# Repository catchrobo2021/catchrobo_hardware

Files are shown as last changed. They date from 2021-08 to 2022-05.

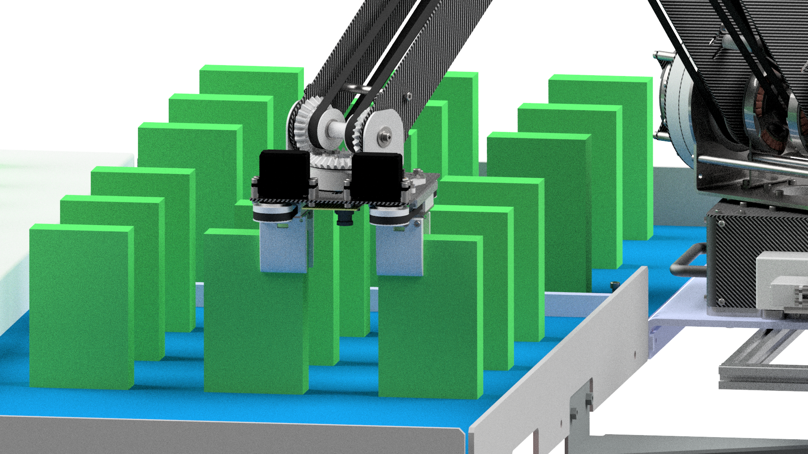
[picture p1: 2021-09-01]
images/assy-robot_with_field_capt2.png

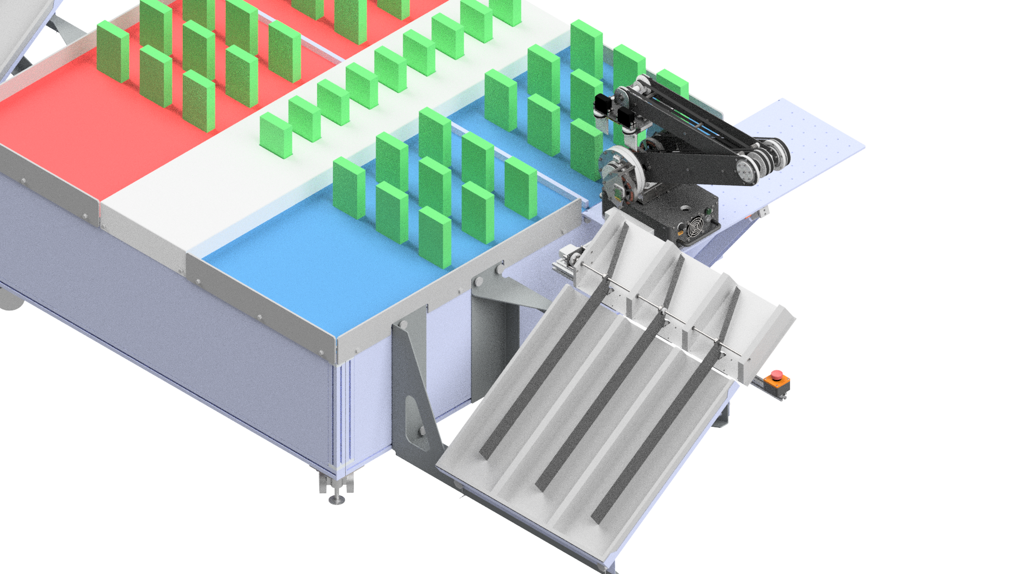
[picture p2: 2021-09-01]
images/assy-robot_with_field_robot_safety.png

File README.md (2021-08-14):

# Catchrobo 2021 Hardware
## 仕様
| | | | J1 | J2 | J3 | J4 | J5 | gripper |
|---|---|---|---|---|---|---|---|---|
| リンク | 質量 | g | 5890.3 | 2323.4 | 1390.5 | 1119.3 | 803.7 | - |
| | 重心位置 | mm | 0.0 | 635.8 | 441.7 | 58.9 | 8.3 | - |
| | 重力トルク（最大） | Nm | 0.0 | 14.5 | 6.0 | 0.6 | 0.1 | - |
| | 慣性モーメント（最小） | g mm^2 | 31614181.0  | 89931948.4  | 22789669.0 | 4522984.0 | 3238892.0 | - |
| | 慣性モーメント（最大） | g mm^2 | 864447935.7 | 268435760.2 | 28833196.4 | 4522984.0 | 3238892.0 | - |
| モータ | トルク定数 | Nm/A | 0.07 | 0.07 | 0.07 | 0.07 | 0.07 | - |
| | KV値 | KV | 105.0 | 105.0 | 105.0 | 105.0 | 105.0 | - |
| | ワット数 | W | 107.0 | 107.0 | 107.0 | 107.0 | 107.0 | - |
| | 端子間抵抗 | Ohms | 0.186 | 0.186 | 0.186 | 0.186 | 0.186 | - |
| | 電源電圧 | V | 24.0 | 24.0 | 24.0 | 24.0 | 24.0 | - |
| | 連続電流 | A | 24.0 | 24.0 | 24.0 | 24.0 | 24.0 | - |
| | 最大トルク | Nm | 1.68 | 1.68 | 1.68 | 1.68 | 1.68 | - |
| | 減速比 | ul | 8.0 | 16.0 | 8.0 | 2.8 | 2.8 | - |
| | 減速後 | Nm | 13.4 | 26.9 | 13.4 | 4.7 | 4.7 | - |
| | ロータ慣性モーメント | g mm^2 | 129469.2 | 129469.2 | 129469.2 | 129469.2  | 129469.2  | - |
| | 最大保持電流（各相） | A | 0.0 | 12.9 | 10.8 | 3.3 | 0.3 | - |
| | 最大消費電流（実効値） | A | 4.5 | 4.5 | 4.5 | 4.5 | 4.5 | - |
| 出力軸 | 加速度リミット（最小） | rad/s/s | 15.4 | 41.1 | 199.8 | 732.7 | 1090.5 | - |
| | 加速度リミット（最大） | rad/s/s | 336.8 | 100.7 | 238.7 | 732.7 | 1090.5 | - |
| | 速度リミット | rad/s or m/sec | 22.5 | 11.3 | 22.5 | 64.3 | 64.3 | 0.113 |
| | 可動域（最小） | deg or m | -160.0 | -90.0 | -160.0 | -90.0 | -160.0 | 0.02 |
| | 可動域（最大） | deg or m | 160.0 | 90.0 | 0.0 | 90.0 | 160.0 | 0.12 |
| 姿勢 | 起動時 | deg or m | 0 | 90 | -160 | 70 | 0 | 0.12 |

# 寸法
* [ロボット寸法](https://github.com/catchrobo2021/catchrobo_hardware/blob/main/assembly_manual/assy-robot.pdf) 
* [フィールド配置図](https://github.com/catchrobo2021/catchrobo_hardware/blob/main/assembly_manual/assy-robot_with_field.pdf)

# 組立図
* [J1](https://github.com/catchrobo2021/catchrobo_hardware/blob/main/assembly_manual/s-assy-unit-j1.pdf)
* [J2](https://github.com/catchrobo2021/catchrobo_hardware/blob/main/assembly_manual/s-assy-unit-j2.pdf)
* [J3](https://github.com/catchrobo2021/catchrobo_hardware/blob/main/assembly_manual/s-assy-unit-j3.pdf)
* [Link0](https://github.com/catchrobo2021/catchrobo_hardware/blob/main/assembly_manual/s-assy-link0.pdf)
* [Link1](https://github.com/catchrobo2021/catchrobo_hardware/blob/main/assembly_manual/s-assy-link1.pdf)
* [Link2](https://github.com/catchrobo2021/catchrobo_hardware/blob/main/assembly_manual/s-assy-link2.pdf)
* [Link3 - Link5](https://github.com/catchrobo2021/catchrobo_hardware/blob/main/assembly_manual/s-assy-link3.pdf)
* [gripper](https://github.com/catchrobo2021/catchrobo_hardware/blob/main/assembly_manual/s-assy-gripper.pdf)

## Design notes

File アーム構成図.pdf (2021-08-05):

## 電源管理ユニット（突入防止回路 / 降圧 / 安全リレー）

USB CAN変換

PC

Joint 1
BLDCモータ

## グリッパ用 マイコン基板

CAN ID = 6

Joint 5

## リミットスイッチ

Joint 4

## リミットスイッチ

Joint 1

## リミットスイッチ

## 非常停止スイッチ

## 電源表示灯

24Vリポ

## バッテリー

Odrive 1

Axis 1
CAN ID = 1

Axis 2
CAN ID = NULL

Joint 1

## エンコーダ

Joint 2
BLDCモータ

Joint 2

## リミットスイッチ

Odrive 2

Axis 1
CAN ID = 2

Axis 2
CAN ID = 3

Joint 2

## エンコーダ

Joint 3
BLDCモータ

Joint 3

## リミットスイッチ

Joint 3

## エンコーダ

Joint Wrist 1
BLDCモータ

Odrive 1

Axis 1
CAN ID = 4

Axis 2
CAN ID = 5

Joint Wrist 1

## エンコーダ

Joint Wrist 2
BLDCモータ

Joint Wrist 2

## エンコーダ

## グリッパ 1 サーボモータ

## グリッパ 2 サーボモータ

## PS3コントローラ

## タッチパネル

DC24V | DC24V | DC24V | DC24V | DC5V

## 手先カメラ

# キャチロボ2021 アーム構成図案

2021/7/21

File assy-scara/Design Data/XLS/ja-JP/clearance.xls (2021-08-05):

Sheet: Ansi Unified Screw Threads
I | Sort Order -1
Fastener Type | Size | Shaft Diameters |  |  | Head Dimensions
 |  | Close | Normal | Loose | Diameter | Depth/Angle | Head Type
Flat Head Machine Screw (82) | #0 | 0.0635 | 0.07 | 0.073 | 0.119 | 82 | 2
Flat Head Machine Screw (82) | #1 | 0.076 | 0.081 | 0.089 | 0.146 | 82 | 2
Flat Head Machine Screw (82) | #2 | 0.089 | 0.096 | 0.1065 | 0.172 | 82 | 2
Flat Head Machine Screw (82) | #3 | 0.104 | 0.11 | 0.12 | 0.199 | 82 | 2
Flat Head Machine Screw (82) | #4 | 0.116 | 0.1285 | 0.136 | 0.225 | 82 | 2
Flat Head Machine Screw (82) | #5 | 0.1285 | 0.136 | 0.154 | 0.252 | 82 | 2
Flat Head Machine Screw (82) | #6 | 0.144 | 0.1495 | 0.1695 | 0.279 | 82 | 2
Flat Head Machine Screw (82) | #8 | 0.1695 | 0.177 | 0.1935 | 0.332 | 82 | 2
Flat Head Machine Screw (82) | #10 | 0.196 | 0.201 | 0.221 | 0.385 | 82 | 2
Flat Head Machine Screw (82) | #12 | 0.221 | 0.228 | 0.246 | 0.438 | 82 | 2
Flat Head Machine Screw (82) | 1/4 | 0.257 | 0.266 | 0.2812 | 0.507 | 82 | 2
Flat Head Machine Screw (82) | 5/16 | 0.323 | 0.332 | 0.3437 | 0.635 | 82 | 2
Flat Head Machine Screw (82) | 3/8 | 0.386 | 0.397 | 0.4062 | 0.762 | 82 | 2
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

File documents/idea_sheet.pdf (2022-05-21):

## 提出締切り：2021/8/31 提出先：キャチロボ事務局

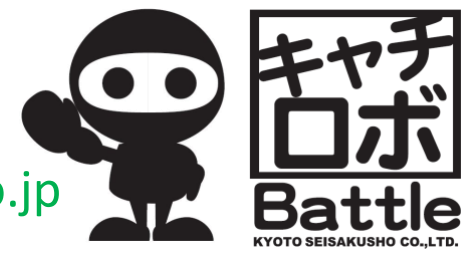
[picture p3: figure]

## E-mail : catchrobo@kyotoss.co.jp

# 早稲田大学 東京工業大学

## Team

# 「安いもんだ…腕の一本くらい」

# 第11回キャチロボバトルコンテスト アイデアシート

## -Member-井上 大雅 岡本 陸 海蔵寺 丘晴 鹿毛 裕太 川村 優登 清水 拓実

## 1.コンセプト・戦略

2

Check Point
✓ ルールブックの違反項目に抵触する戦略を立てていませんか？

◆ 全体のコンセプト
4自由度の水平多関節型ロボットアームを自動制御し、高速かつ 高精度にワークを回収，配置する．

◆ 設計方針
- ロボットアーム
- 関節にはDCブラシレスモータと樹脂製減速機からなる準 ダイレクトドライブアクチュエータを採用する．コストを 抑えつつ，十分なトルクと位置決め精度を確保する．
- 関節アクチュエータをできるだけ手前に配置し，そこから タイミングベルトにより伝動する構成とする．これにより 慣性モーメントを最小に抑え，十分な加速性能を確保でき るようにする．
- ハンドは同時に2つのワークを回収できる設計としタクト タイムを短縮する．
- シューター
- ワークを整列させるためにシューティングボックス上空に 展開するガイド機構と，ワークの姿勢を整えてシューティ ングボックスに投入するワイパー機構の2つから構成され る．
- ワイパー機構は，ロボットアームの位置決め誤差を許容し ，確実にワークを投入できるよう補助を行う．
- ガイド機構が動作しない場合に備え，電源を遮断するとカ ウンタウェイトによりガイドが自動で初期姿勢に戻る構造 にする．

◆ 制御方針
- 自動制御
- 100%自動
- オブジェクトの間を縫うような衝突回避
- ビスコが微動だにしない加減速
- 手先カメラで事故対応も万全

## 2.ロボットの構成

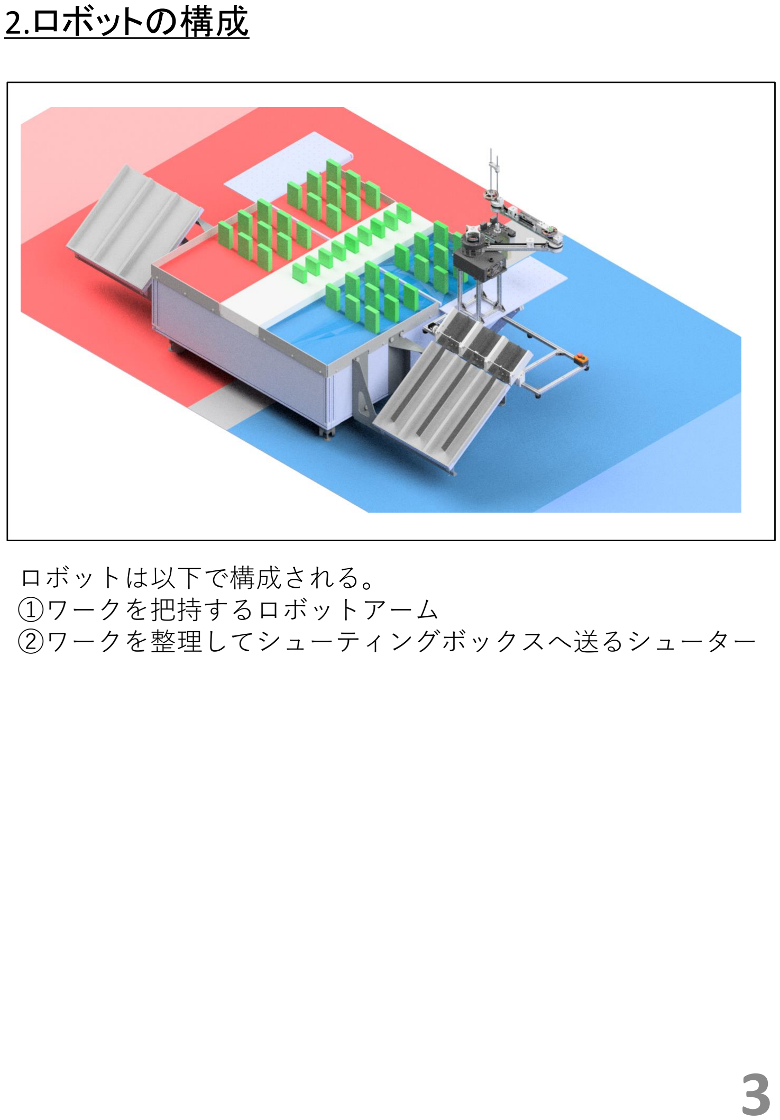
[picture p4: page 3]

3

構成図

ロボットは以下で構成される。
①ワークを把持するロボットアーム
②ワークを整理してシューティングボックスへ送るシューター

## 3.ロボットユニット詳細

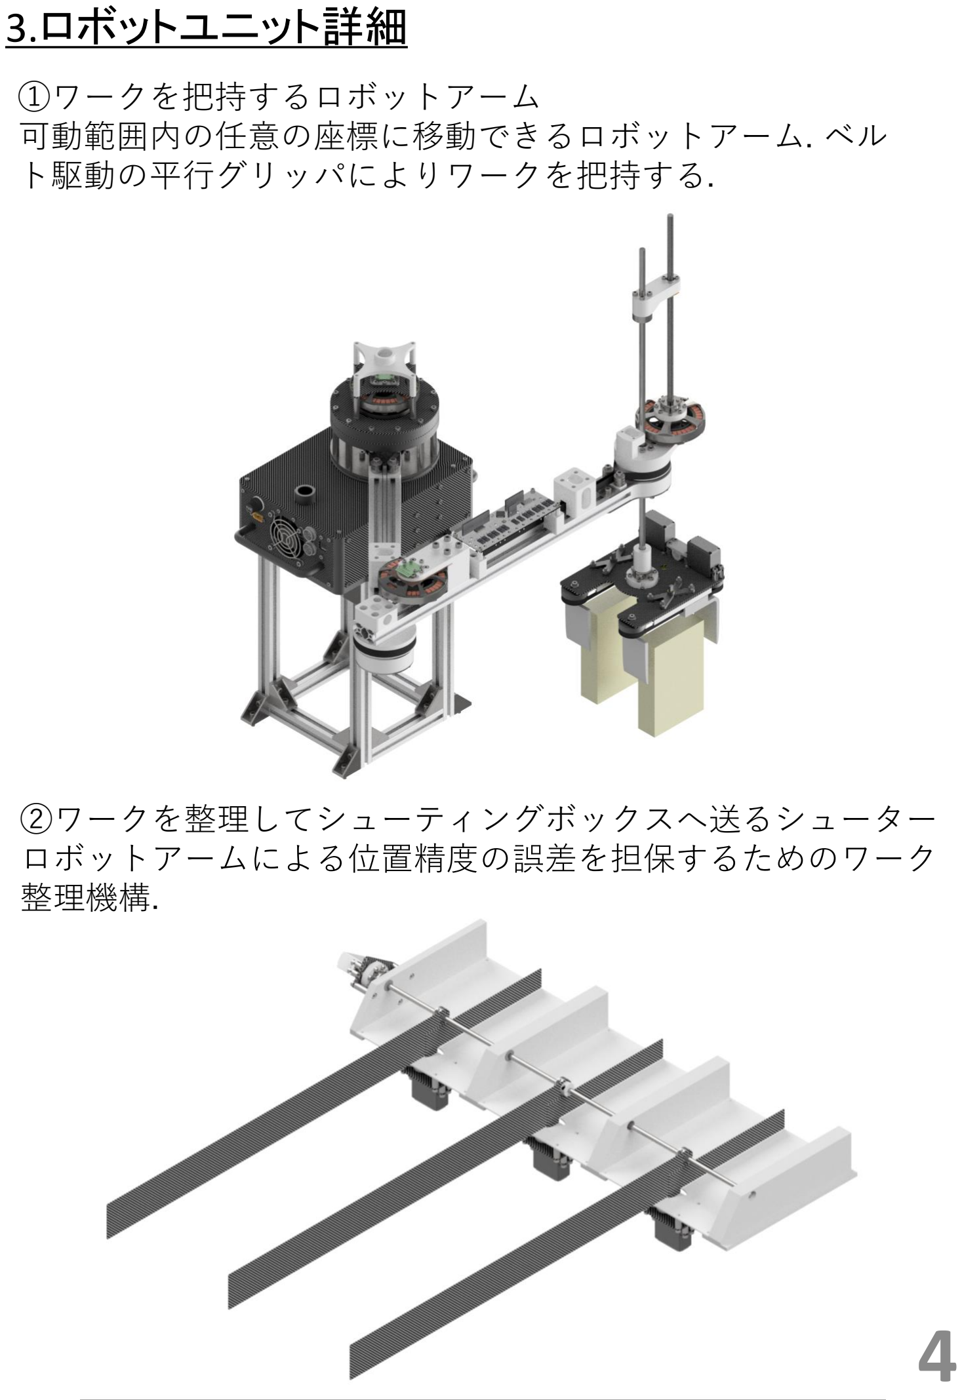
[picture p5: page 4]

4

①ワークを把持するロボットアーム
可動範囲内の任意の座標に移動できるロボットアーム. ベル ト駆動の平行グリッパによりワークを把持する.

②ワークを整理してシューティングボックスへ送るシューター ロボットアームによる位置精度の誤差を担保するためのワーク 整理機構.

## 4.ロボット主要寸法（スタート時）

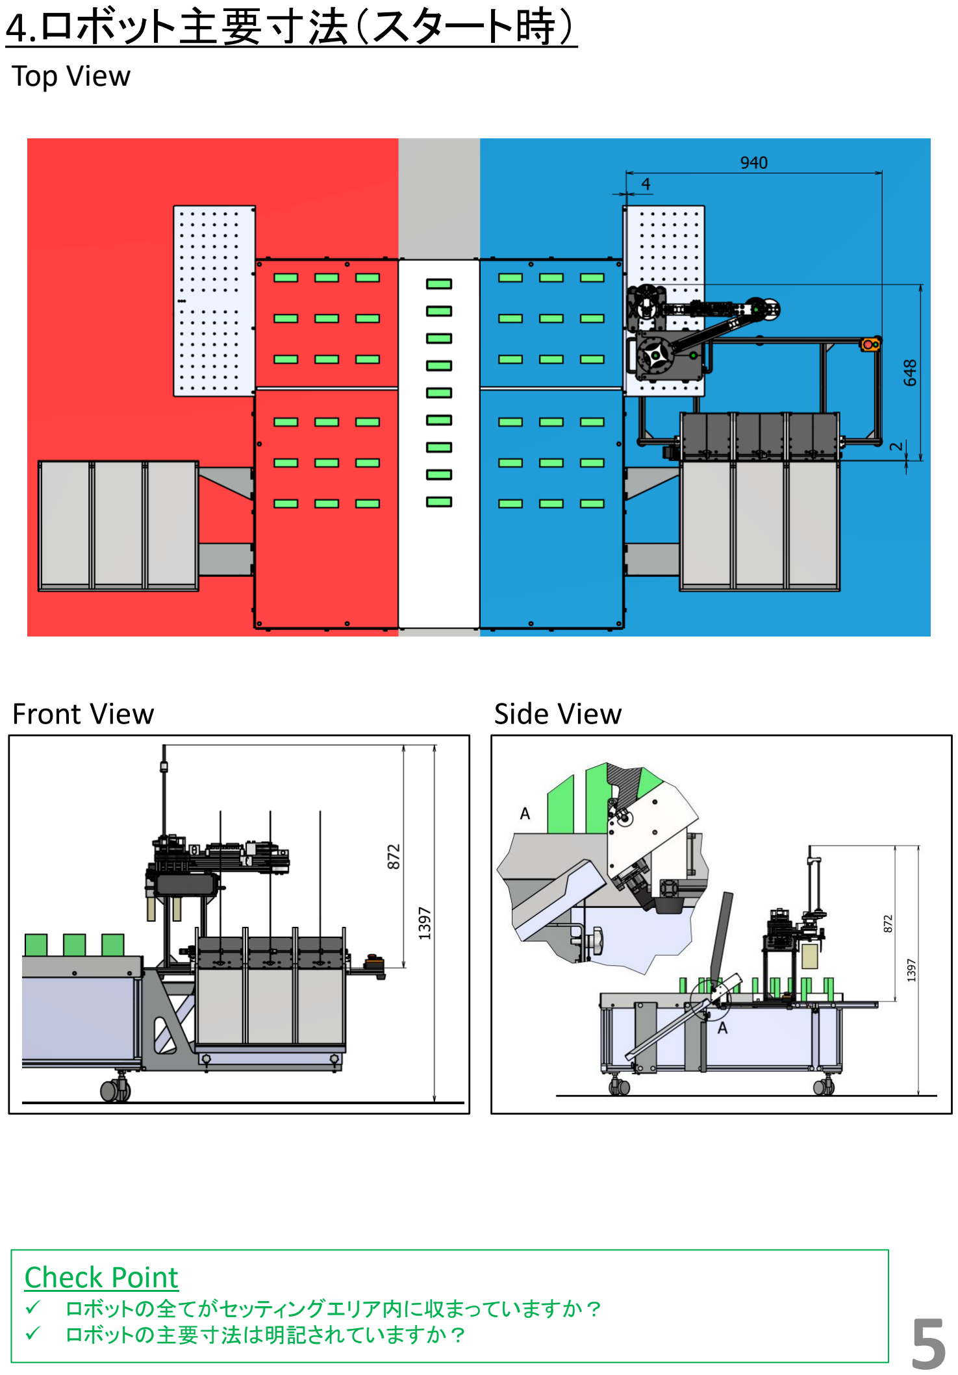
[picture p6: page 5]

Check Point
✓ | ロボットの全てがセッティングエリア内に収まっていますか？
✓ | ロボットの主要寸法は明記されていますか？

Top View

Front View | Side View

5

## 4.ロボット主要寸法（可動範囲）

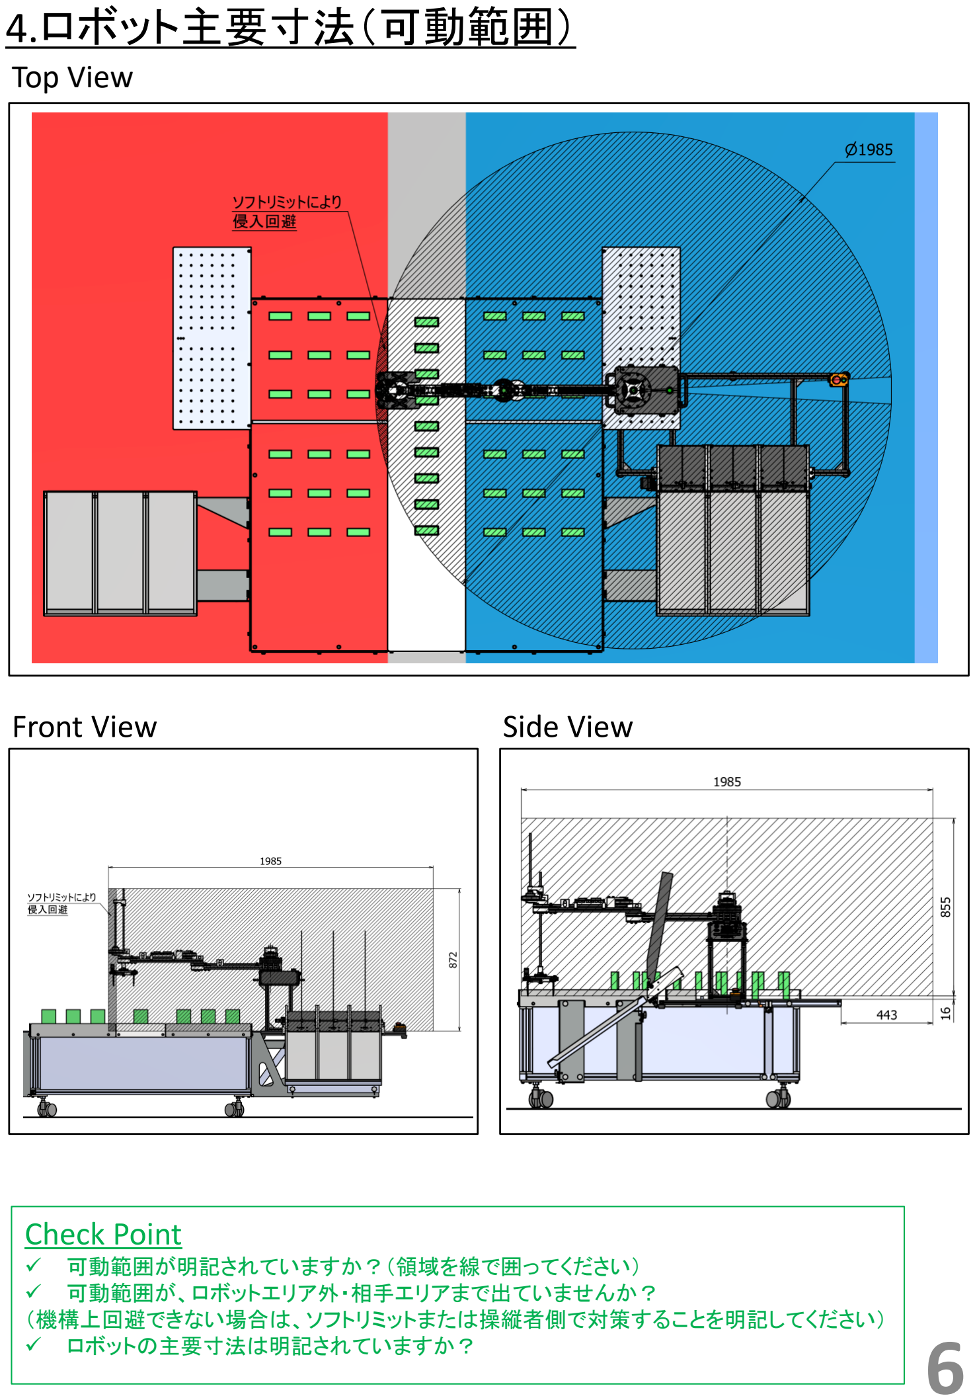
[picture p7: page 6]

Check Point
✓ | 可動範囲が明記されていますか？（領域を線で囲ってください）
✓ | 可動範囲が、ロボットエリア外・相手エリアまで出ていませんか？
（機構上回避できない場合は、ソフトリミットまたは操縦者側で対策することを明記してください） ✓ ロボットの主要寸法は明記されていますか？

Top View

Front View | Side View

6

## 5.ワークのハンドリング方法（ワークエリア内）

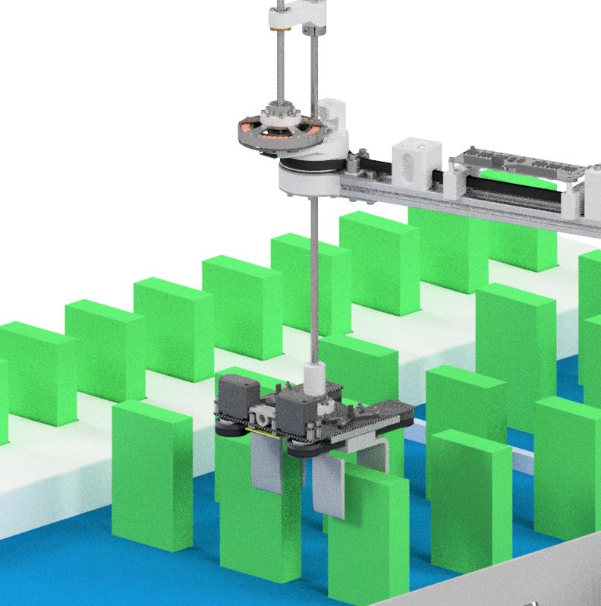
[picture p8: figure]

Check Point
✓ | 突刺す、接着するなど、ワークを破損させる方法でハンドリングしていませんか？ | 7

グリッパによりワークを2つまとめて把持する．

## 5.ワークのハンドリング方法（共通エリア内）

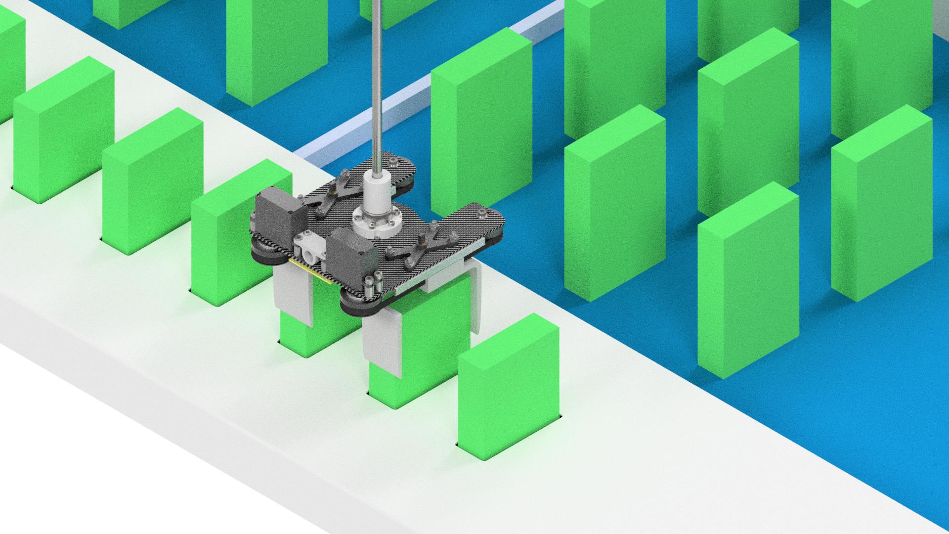
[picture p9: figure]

Check Point
✓ | 突刺す、接着するなど、ワークを破損させる方法でハンドリングしていませんか？ | 8

グリッパによりワークを2つまとめて把持する．

## 6.得点に関する条件の達成方法（得点条件）

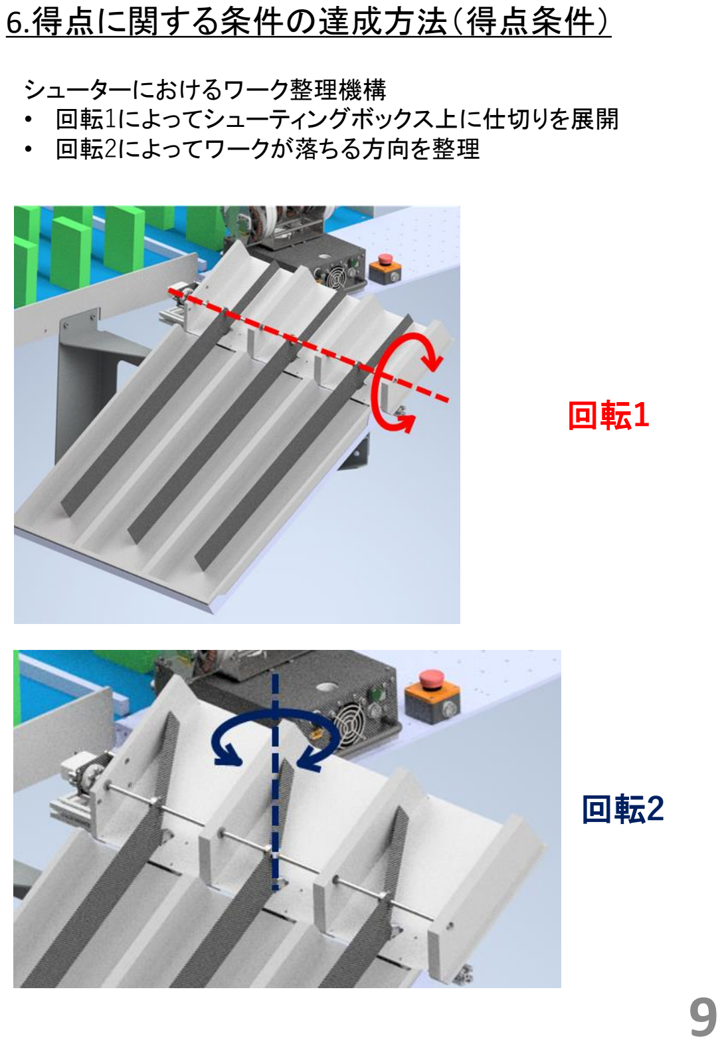
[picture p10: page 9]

9

シューターにおけるワーク整理機構
- 回転1によってシューティングボックス上に仕切りを展開
- 回転2によってワークが落ちる方向を整理

回転1

回転2

## 6.得点に関する条件の達成方法（ボーナス条件A）

10

- ワーク整理機構によってワークを期待する配置に整理する.
- ワークの表裏はアームロボットの手首の回転によって反転す る.

## 6.得点に関する条件の達成方法（ボーナス条件B）

11

- ボーナス条件Aと同様

## 7.非常停止ボタンと動力電源表示灯

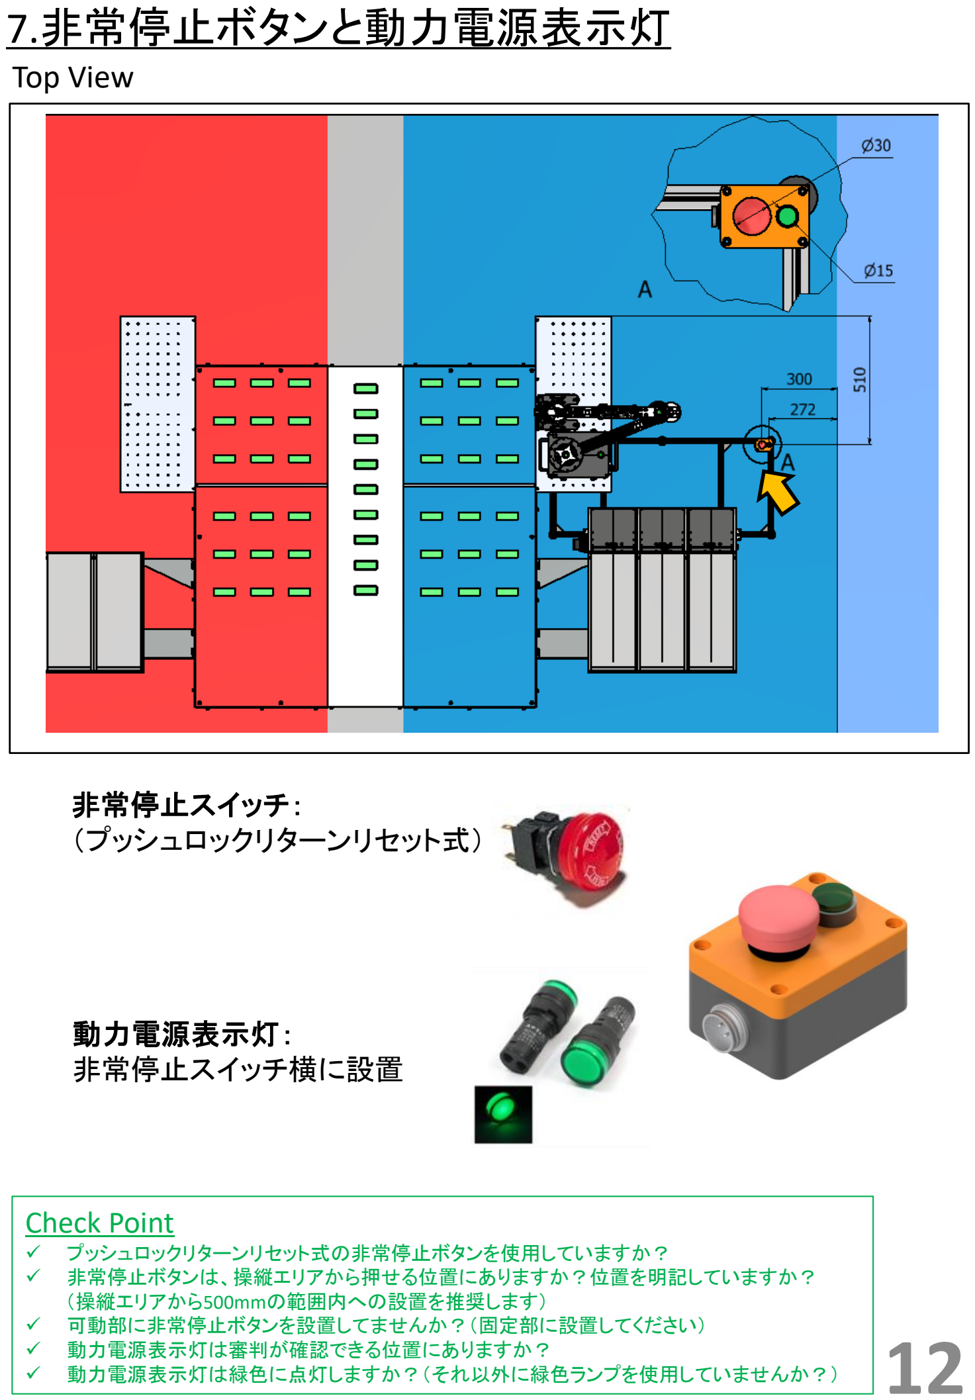
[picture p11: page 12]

Check Point
✓ | プッシュロックリターンリセット式の非常停止ボタンを使用していますか？
✓ | 非常停止ボタンは、操縦エリアから押せる位置にありますか？位置を明記していますか？
| （操縦エリアから500mmの範囲内への設置を推奨します）
✓ | 可動部に非常停止ボタンを設置してませんか？（固定部に設置してください）
✓ | 動力電源表示灯は審判が確認できる位置にありますか？
✓ | 動力電源表示灯は緑色に点灯しますか？（それ以外に緑色ランプを使用していませんか？）

Top View

12

非常停止スイッチ：
（プッシュロックリターンリセット式）

動力電源表示灯：
非常停止スイッチ横に設置

## 8.フィールドへのロボット固定方法

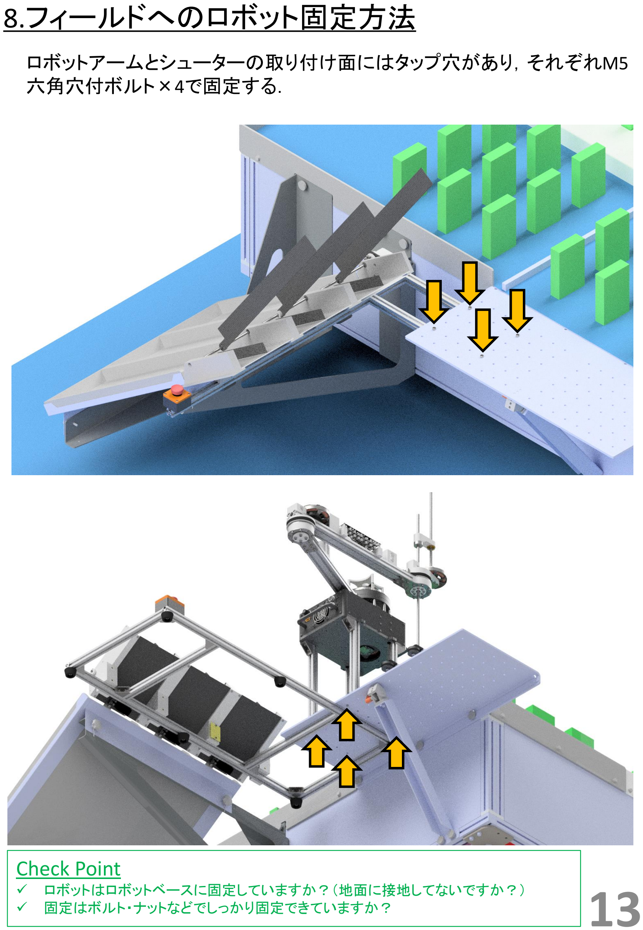
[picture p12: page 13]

Check Point
✓ | ロボットはロボットベースに固定していますか？（地面に接地してないですか？）
✓ | 固定はボルト・ナットなどでしっかり固定できていますか？ | 13

ロボットアームとシューターの取り付け面にはタップ穴があり，それぞれM5 六角穴付ボルト×4で固定する．

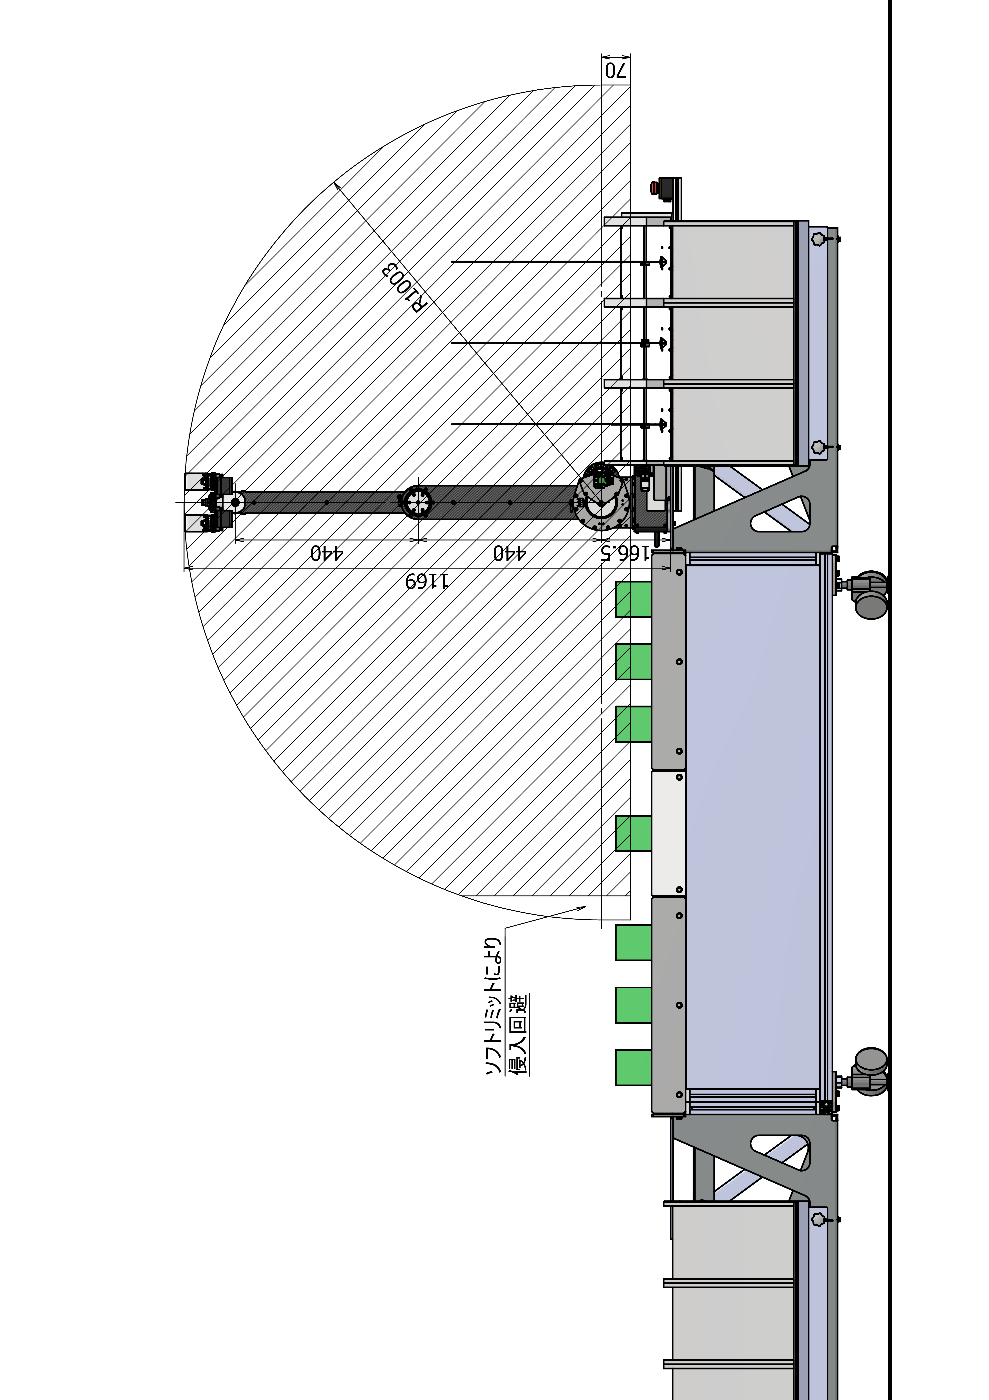
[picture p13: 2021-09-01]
images/assy-robot_with_field_front_rom.png

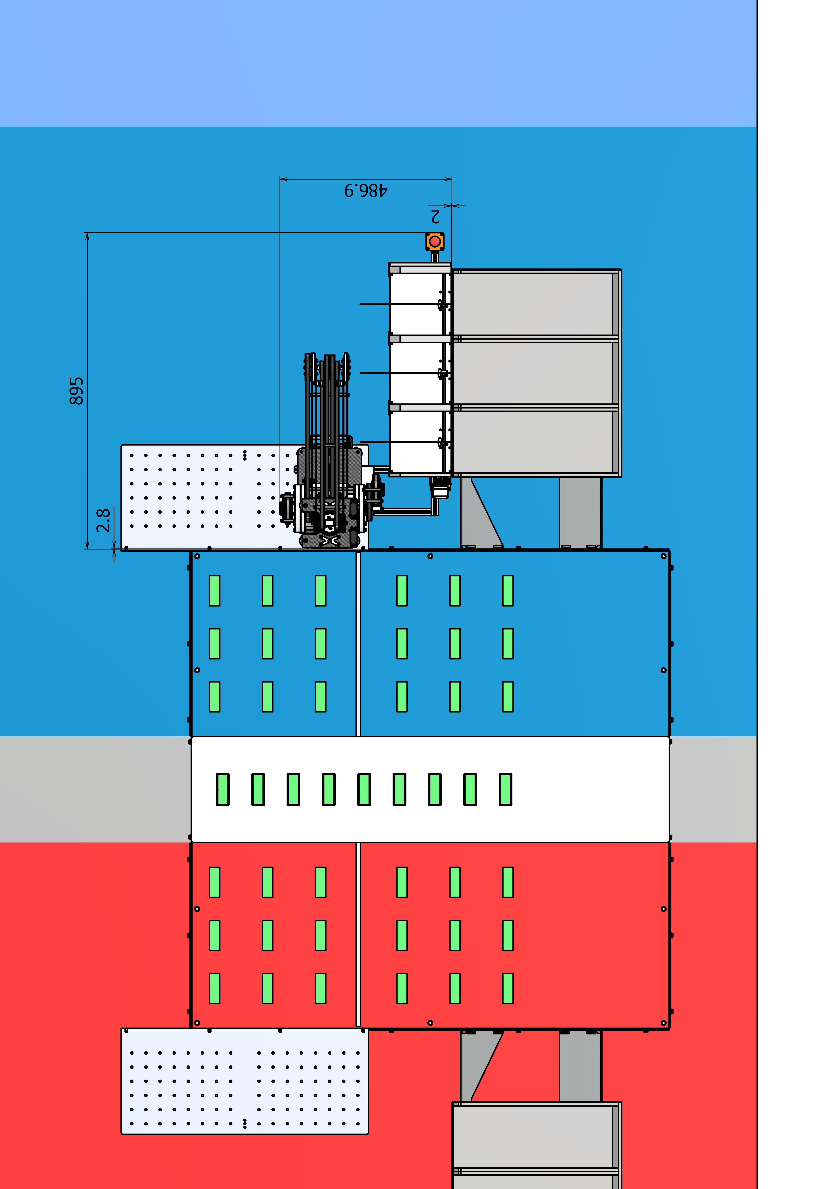
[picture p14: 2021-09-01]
images/assy-robot_with_field_dimensions.png

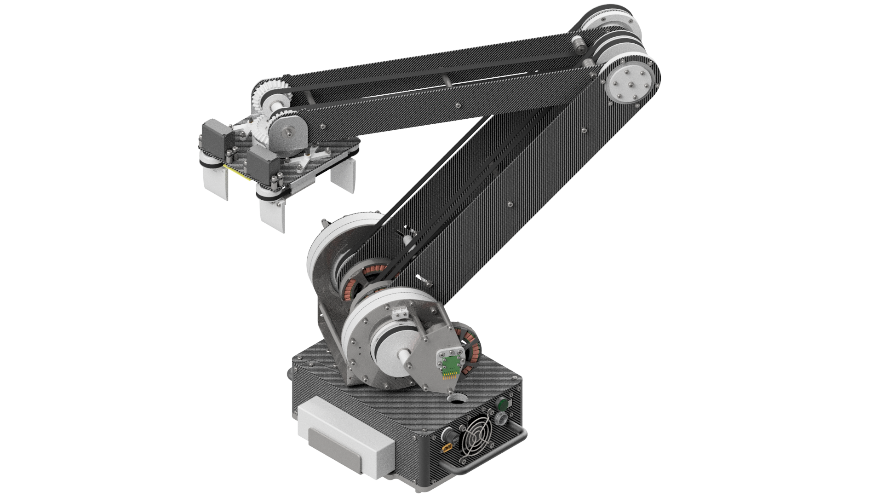
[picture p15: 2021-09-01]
images/assy-robot.png

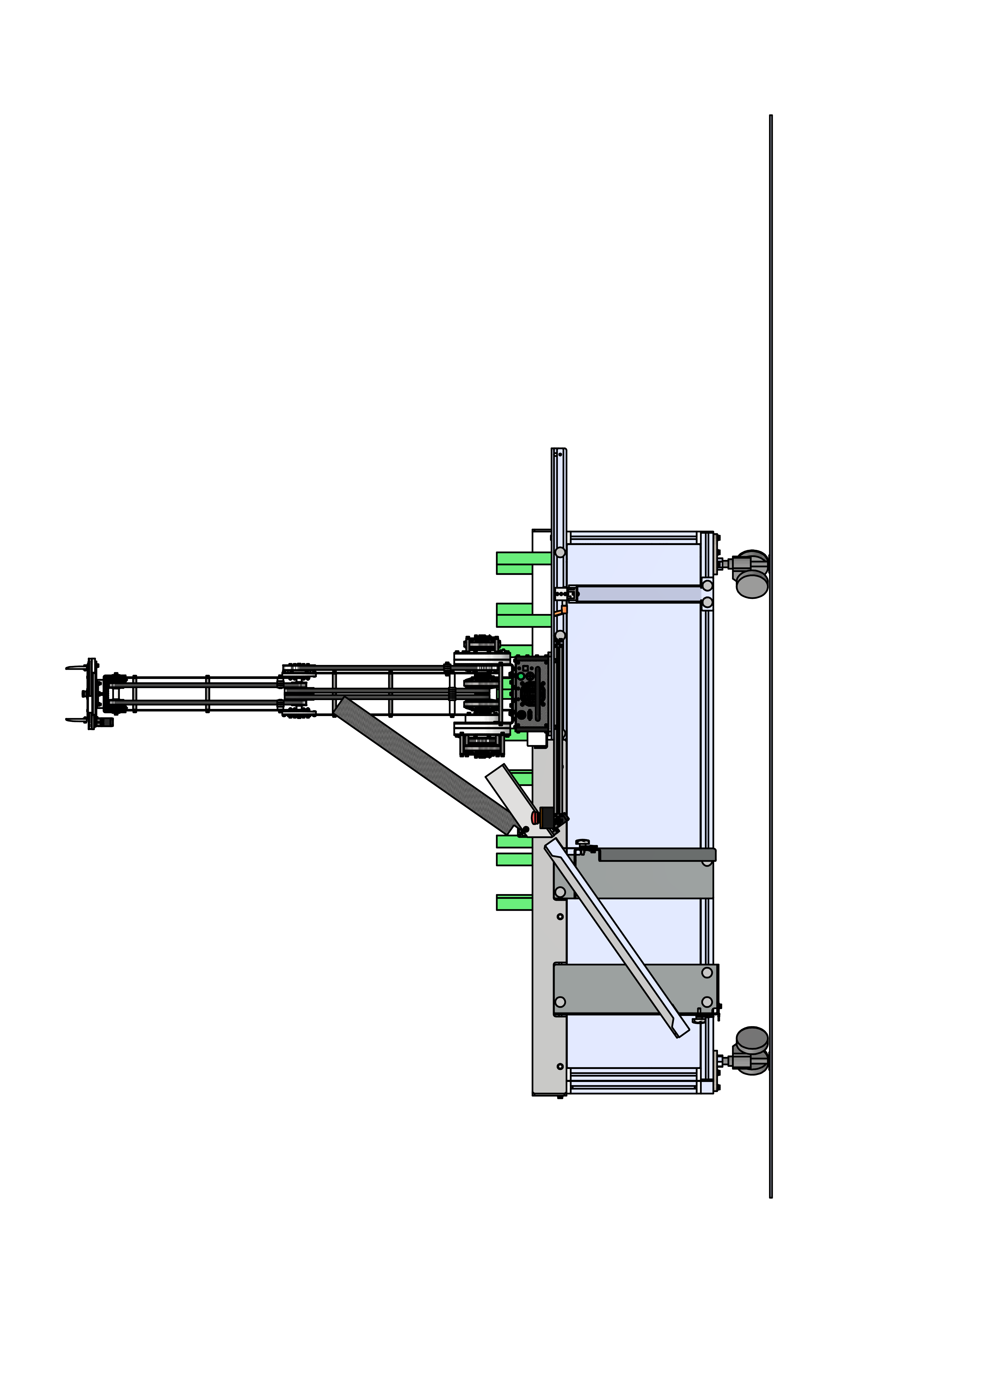
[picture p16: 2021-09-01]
images/assy-robot_with_field_side_rom.png

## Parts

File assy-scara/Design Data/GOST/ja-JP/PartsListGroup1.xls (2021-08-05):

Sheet: Лист 1
Инв. № подл |  |  |  | Подп. и дата | Взам. инв. № | Инв. № дубл. |  |  | Подп. и дата
Формат | Зона | Поз. | Обозначение |  |  |  | Наименование |  |  |  |  |  | Кол. на исполнение
 |  |  |  |  |  |  |  |  |  |  |  | Лит.
 |  |  |  |  |  |  |  |  |  |  |  | Код
 |  |  |  |  |  |  |  | Изм. | Лист | № докум | Подпись |  | Дата
 |  |  |  |  |  |  |  | Разраб.
 |  |  |  |  |  |  |  | Пров.
 |  |  |  |  |  |  |  | Н.контр
 |  |  |  |  |  |  |  | Утв.
 |  |  |  |  |  |  |  |  |  |  |  |  |  | Копировал

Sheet: Лист 2
Инв. № подл |  |  |  | Подп. и дата | Взам. инв. № | Инв. № дубл. |  |  | Подп. и дата
Формат | Зона | Поз. | Обозначение |  |  |  | Наименование |  |  |  |  | Кол. на исполнение
 |  |  |  |  |  |  |  | Изм. | Лист | № докум. | Подп. | Дата
 |  |  |  |  |  |  |  |  |  |  |  |  | Копировал
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

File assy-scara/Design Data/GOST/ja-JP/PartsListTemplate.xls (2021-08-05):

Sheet: Лист 1
 | Формат | Зона |  | Поз. |  | Обозначение |  |  |  | Наименование |  |  |  | Кол. | Приме-чание
Подп. и дата
Инв. № дубл.
Взам. инв. №
Подп. и дата
 | Изм. |  | Лист |  | № докум |  | Подпись | Дата
Инв. № подл | Разраб. |  |  |  |  |  |  |  |  |  | Литера |  | Лист |  |  | Листов
 | Пров.
 | Н.контр
 | Утв.
 |  |  |  |  |  |  |  |  | Копировал |  |  | Формат А4

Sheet: Лист 2
 | Формат | Зона |  | Поз. |  | Обозначение |  |  |  | Наименование |  | Кол. | Приме-чание
Подп. и дата
Инв. № дубл.
Взам. инв. №
Подп. и дата
Инв. № подл
 | Изм. |  | Лист |  | № докум. |  | Подп. |  | Дата
 |  |  |  |  |  |  |  | Копировал |  |  | Формат А4
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

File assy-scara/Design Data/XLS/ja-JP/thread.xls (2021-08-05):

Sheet: Inch Tapping Threads
I Q X | Inch Tapping Threads |  | Sort Order - 5 |  | External |  |  |  |  |  |  | Internal
 |  |  |  |  |  | Major Dia |  | Pitch Dia |  | Minor Dia |  |  | Minor Dia |  | Pitch Dia |  | Major Dia |  | Tap Drill
Size | Size Suffix | Thread Designation | Custom Thread Designation | TPI | Class | Max | Min | Max | Min | Max | Min | Class | Min | Max | Min | Max | Min | Max | Basic
0.0600 |  | 0-48 | 0-48 | 48 | 2B | 0.0600 | 0.0540 | 0.0480 | 0.0435 | 0.0360 | 0.0330
0.0730 |  | 1-42 | 1-42 | 42 | 2B | 0.0750 | 0.0690 | 0.0620 | 0.0575 | 0.0490 | 0.0460
0.0860 |  | 2-32 | 2-32 | 32 | 2B | 0.0880 | 0.0820 | 0.0760 | 0.0710 | 0.0640 | 0.0600
0.0990 |  | 3-28 | 3-28 | 28 | 2B | 0.1010 | 0.0950 | 0.0880 | 0.0830 | 0.0750 | 0.0710
0.1120 |  | 4-24 | 4-24 | 24 | 2B | 0.1140 | 0.1080 | 0.1000 | 0.0950 | 0.0860 | 0.0820
0.1250 |  | 5-20 | 5-20 | 20 | 2B | 0.1300 | 0.1230 | 0.1120 | 0.1065 | 0.0940 | 0.0900
0.1380 |  | 6-20 | 6-20 | 20 | 2B | 0.1390 | 0.1320 | 0.1215 | 0.1155 | 0.1040 | 0.0990
0.1510 |  | 7-19 | 7-19 | 19 | 2B | 0.1540 | 0.1470 | 0.1345 | 0.1280 | 0.1150 | 0.1090
0.1640 |  | 8-18 | 8-18 | 18 | 2B | 0.1660 | 0.1590 | 0.1440 | 0.1375 | 0.1220 | 0.1160
0.1900 |  | 10-16 | 10-16 | 16 | 2B | 0.1890 | 0.1820 | 0.1650 | 0.1585 | 0.1410 | 0.1350
0.2160 |  | 12-14 | 12-14 | 14 | 2B | 0.2150 | 0.2080 | 0.1895 | 0.1825 | 0.1640 | 0.1570
0.2420 |  | 14-14 | 14-14 | 14 | 2B | 0.2410 | 0.2340 | 0.2130 | 0.2060 | 0.1850 | 0.1780
0.2500 |  | 1/4-14 | 1/4-14 | 14 | 2B | 0.2460 | 0.2370 | 0.2190 | 0.2110 | 0.1920 | 0.1850
0.3125 |  | 5/16-12 | 5/16-12 | 12 | 2B | 0.3150 | 0.3060 | 0.2795 | 0.2710 | 0.2440 | 0.2360
0.3750 |  | 3/8-12 | 3/8-12 | 12 | 2B | 0.3800 | 0.3710 | 0.3445 | 0.3350 | 0.3090 | 0.2990
0.4375 |  | 7/16-10 | 7/16-10 | 10 | 2B | 0.4400 | 0.4290 | 0.3995 | 0.3890 | 0.3590 | 0.3490
0.5000 |  | 1/2-10 | 1/2-10 | 10 | 2B | 0.5040 | 0.4930 | 0.4635 | 0.4530 | 0.4230 | 0.4130

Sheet: Metric Forming Screw Threads
M P X | Metric Forming Screw Threads |  | Sort Order - 6 |  | External |  |  |  |  |  |  | Internal
 |  |  |  |  |  | Major Dia |  | Pitch Dia |  | Minor Dia |  |  | Minor Dia |  | Pitch Dia |  | Major Dia |  | Tap Drill
Size | Size Suffix | Thread Designation | Custom Thread Designation | Pitch | Class | Max | Min | Max | Min | Max | Min | Class | Min | Max | Min | Max | Min | Max | Basic
1.5 |  | 1.5x0.5 | 1.5x0.5 | 0.5 | 6g | 1.520 | 1.380 | 1.215 | 1.110 | 0.910 | 0.840
1.5 |  | ST1.5x0.5 | ST1.5x0.5 | 0.5 | 6g | 1.520 | 1.380 | 1.215 | 1.110 | 0.910 | 0.840
1.9 |  | 1.9x0.6 | 1.9x0.6 | 0.6 | 6g | 1.900 | 1.760 | 1.570 | 1.465 | 1.240 | 1.170
1.9 |  | ST1.9x0.6 | ST1.9x0.6 | 0.6 | 6g | 1.900 | 1.760 | 1.570 | 1.465 | 1.240 | 1.170
2.2 |  | 2.2x0.8 | 2.2x0.8 | 0.8 | 6g | 2.240 | 2.100 | 1.935 | 1.810 | 1.630 | 1.520
2.2 |  | ST2.2x0.8 | ST2.2x0.8 | 0.8 | 6g | 2.240 | 2.100 | 1.935 | 1.810 | 1.630 | 1.520
2.6 |  | 2.6x0.9 | 2.6x0.9 | 0.9 | 6g | 2.570 | 2.430 | 2.235 | 2.115 | 1.900 | 1.800
2.6 |  | ST2.6x0.9 | ST2.6x0.9 | 0.9 | 6g | 2.570 | 2.430 | 2.235 | 2.115 | 1.900 | 1.800
2.9 |  | 2.9x1 | 2.9x1 | 1 | 6g | 2.900 | 2.760 | 2.540 | 2.420 | 2.180 | 2.080
2.9 |  | 2.9x1.1 | 2.9x1.1 | 1.1 | 6g | 2.900 | 2.760 | 2.540 | 2.420 | 2.180 | 2.080
2.9 |  | ST2.9x1.1 | ST2.9x1.1 | 1.1 | 6g | 2.900 | 2.760 | 2.540 | 2.420 | 2.180 | 2.080
2.9 |  | 2.9x1.3 | 2.9x1.3 | 1.3 | 6g | 2.900 | 2.720 | 2.540 | 2.355 | 1.890 | 1.700
2.9 |  | 2.9x1.4 | 2.9x1.4 | 1.4 | 6g | 2.900 | 2.720 | 2.340 | 2.175 | 1.780 | 1.630
3.3 |  | 3.3x1.3 | 3.3x1.3 | 1.3 | 6g | 3.300 | 3.120 | 2.795 | 2.665 | 2.290 | 2.210
3.3 |  | ST3.3x1.3 | ST3.3x1.3 | 1.3 | 6g | 3.300 | 3.120 | 2.795 | 2.665 | 2.290 | 2.210
3.5 |  | 3.5x1.3 | 3.5x1.3 | 1.3 | 6g | 3.530 | 3.350 | 3.085 | 2.930 | 2.640 | 2.510
3.5 |  | ST3.5x1.3 | ST3.5x1.3 | 1.3 | 6g | 3.530 | 3.350 | 3.085 | 2.930 | 2.640 | 2.510
3.5 |  | 3.5x1.6 | 3.5x1.6 | 1.6 | 6g | 3.530 | 3.350 | 2.920 | 2.755 | 2.310 | 2.160
3.5 |  | 3.5x3.2 | 3.5x3.2 | 3.2 | 6g | 3.530 | 3.310 | 2.800 | 2.600 | 2.070 | 1.890
3.9 |  | 3.9x1.3 | 3.9x1.3 | 1.3 | 6g | 3.910 | 3.730 | 3.415 | 3.250 | 2.920 | 2.770
3.9 |  | ST3.9x1.3 | ST3.9x1.3 | 1.3 | 6g | 3.910 | 3.730 | 3.415 | 3.250 | 2.920 | 2.770
3.9 |  | 3.9x1.6 | 3.9x1.6 | 1.6 | 6g | 3.910 | 3.730 | 3.300 | 3.135 | 2.690 | 2.540
3.9 |  | 3.9x3.2 | 3.9x3.2 | 3.2 | 6g | 3.910 | 3.690 | 3.180 | 2.980 | 2.450 | 2.270
4.2 |  | 4.2x1.4 | 4.2x1.4 | 1.4 | 6g | 4.220 | 4.040 | 3.660 | 3.495 | 3.100 | 2.950
4.2 |  | ST4.2x1.4 | ST4.2x1.4 | 1.4 | 6g | 4.220 | 4.040 | 3.660 | 3.495 | 3.100 | 2.950
4.2 |  | 4.2x1.6 | 4.2x1.6 | 1.6 | 6g | 4.220 | 4.040 | 3.610 | 3.445 | 3.000 | 2.850
4.2 |  | 4.2x3.2 | 4.2x3.2 | 3.2 | 6g | 4.220 | 4.000 | 3.380 | 3.180 | 2.540 | 2.360
4.8 |  | 4.8x1.6 | 4.8x1.6 | 1.6 | 6g | 4.800 | 4.620 | 4.190 | 4.025 | 3.580 | 3.430
4.8 |  | ST4.8x1.6 | ST4.8x1.6 | 1.6 | 6g | 4.800 | 4.620 | 4.190 | 4.025 | 3.580 | 3.430
4.8 |  | 4.8x1.8 | 4.8x1.8 | 1.8 | 6g | 4.800 | 4.620 | 4.065 | 3.885 | 3.330 | 3.150
4.8 |  | 4.8x3.2 | 4.8x3.2 | 3.2 | 6g | 4.800 | 4.580 | 3.960 | 3.760 | 3.120 | 2.940
5.5 |  | 5.5x1.8 | 5.5x1.8 | 1.8 | 6g | 5.460 | 5.280 | 4.815 | 4.635 | 4.170 | 3.990
5.5 |  | ST5.5x1.8 | ST5.5x1.8 | 1.8 | 6g | 5.460 | 5.280 | 4.815 | 4.635 | 4.170 | 3.990
6.3 |  | 6.3x1.8 | 6.3x1.8 | 1.8 | 6g | 6.250 | 6.030 | 5.565 | 5.365 | 4.880 | 4.700
6.3 |  | ST6.3x1.8 | ST6.3x1.8 | 1.8 | 6g | 6.250 | 6.030 | 5.565 | 5.365 | 4.880 | 4.700
8.0 |  | 8x2.1 | 8x2.1 | 2.1 | 6g | 8.000 | 7.780 | 7.100 | 6.885 | 6.200 | 5.990
8.0 |  | ST8x2.1 | ST8x2.1 | 2.1 | 6g | 8.000 | 7.780 | 7.100 | 6.885 | 6.200 | 5.990
9.5 |  | 9.5x2.1 | 9.5x2.1 | 2.1 | 6g | 9.650 | 9.430 | 8.750 | 8.510 | 7.850 | 7.590
9.5 |  | ST9.5x2.1 | ST9.5x2.1 | 2.1 | 6g | 9.650 | 9.430 | 8.750 | 8.510 | 7.850 | 7.590

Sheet: ISO Pipe Threads
M Q | ISO Pipe Threads |  | Sort Order - 9 |  | External |  |  |  |  |  |  | Internal
 |  |  |  |  |  | Major Dia |  | Pitch Dia |  | Minor Dia |  |  | Minor Dia |  | Pitch Dia |  | Major Dia |  | Tap Drill | Thread Depth | Thread Runouts
Size | Size Suffix | Thread Designation | Custom Thread Designation | TPI | Class | Max | Min | Max | Min | Max | Min | Class | Min | Max | Min | Max | Min | Max | Basic
7.723 |  | G7.723x0.907 | G 1/16 | 28 | A | 7.723 | 7.509 | 7.142 | 7.035 | 6.561 |  |  | 6.561 | 6.834 | 7.142 | 7.249 | 7.723 |  | 1.5875 | 15.446 | 4.5000
7.723 |  | G7.723x0.907 | G 1/16 | 28 | B | 7.723 | 7.509 | 7.142 | 6.928 | 6.561
9.728 |  | G9.728x0.907 | G 1/8 | 28 | A | 9.728 | 9.514 | 9.147 | 9.040 | 8.566 |  |  | 8.566 | 8.848 | 9.147 | 9.254 | 9.728 |  | 3.1750 | 19.456 | 4.5000
9.728 |  | G9.728x0.907 | G 1/8 | 28 | B | 9.728 | 9.514 | 9.147 | 8.933 | 8.566
13.157 |  | G13.157x1.337 | G 1/4 | 19 | A | 13.157 | 12.907 | 12.301 | 12.176 | 11.445 |  |  | 11.445 | 11.89 | 12.301 | 12.426 | 13.157 |  | 6.3500 | 26.314 | 6.5000
13.157 |  | G13.157x1.337 | G 1/4 | 19 | B | 13.157 | 12.907 | 12.301 | 12.051 | 11.445
16.662 |  | G16.662x1.337 | G 3/8 | 19 | A | 16.662 | 16.412 | 15.806 | 15.681 | 14.950 |  |  | 14.95 | 15.395 | 15.806 | 15.931 | 16.662 |  | 9.5250 | 33.324 | 6.5000
16.662 |  | G16.662x1.337 | G 3/8 | 19 | B | 16.662 | 16.412 | 15.806 | 15.556 | 14.950
20.955 |  | G20.955x1.814 | G 1/2 | 14 | A | 20.955 | 20.671 | 19.793 | 19.651 | 18.631 |  |  | 18.631 | 19.172 | 19.793 | 19.935 | 20.955 |  | 12.7000 | 41.910 | 8.5000
20.955 |  | G20.955x1.814 | G 1/2 | 14 | B | 20.955 | 20.671 | 19.793 | 19.509 | 18.631
22.911 |  | G22.911x1.814 | G 5/8 | 14 | A | 22.911 | 22.627 | 21.749 | 21.607 | 20.587 |  |  | 20.587 | 21.128 | 21.749 | 21.891 | 22.911 |  |  | 45.822 | 8.5000
22.911 |  | G22.911x1.814 | G 5/8 | 14 | B | 22.911 | 22.627 | 21.749 | 21.465 | 20.587
26.441 |  | G26.441x1.814 | G 3/4 | 14 | A | 26.441 | 26.157 | 25.279 | 25.137 | 24.117 |  |  | 24.117 | 24.658 | 25.279 | 25.421 | 26.441 |  | 15.8750 | 52.882 | 8.5000
26.441 |  | G26.441x1.814 | G 3/4 | 14 | B | 26.441 | 26.157 | 25.279 | 24.995 | 24.117
30.201 |  | G30.201x1.814 | G 7/8 | 14 | A | 30.201 | 29.917 | 29.039 | 28.897 | 27.877 |  |  | 27.877 | 28.418 | 29.039 | 29.181 | 30.201 |  | 22.2250 | 60.402 | 8.5000
30.201 |  | G30.201x1.814 | G 7/8 | 14 | B | 30.201 | 29.917 | 29.039 | 28.755 | 27.877
33.249 |  | G33.249x2.309 | G 1 | 11 | A | 33.249 | 32.889 | 31.770 | 31.590 | 30.291 |  |  | 30.291 | 30.931 | 31.77 | 31.95 | 33.249 |  | 25.4000 | 66.498 | 10.0000
33.249 |  | G33.249x2.309 | G 1 | 11 | B | 33.249 | 32.889 | 31.770 | 31.410 | 30.291
37.897 |  | G37.897x2.309 | G 1 1/8 | 11 | A | 37.897 | 37.537 | 36.418 | 36.238 | 34.939 |  |  | 34.939 | 35.579 | 36.418 | 36.598 | 37.897 |  | 28.5750 | 75.794 | 10.0000
37.897 |  | G37.897x2.309 | G 1 1/8 | 11 | B | 37.897 | 37.537 | 36.418 | 36.058 | 34.939
41.910 |  | G41.91x2.309 | G 1 1/4 | 11 | A | 41.910 | 41.550 | 40.431 | 40.251 | 38.952 |  |  | 38.952 | 39.592 | 40.431 | 40.611 | 41.910 |  | 31.7500 | 83.820 | 10.0000
41.910 |  | G41.91x2.309 | G 1 1/4 | 11 | B | 41.910 | 41.550 | 40.431 | 40.071 | 38.952
47.803 |  | G47.803x2.309 | G 1 1/2 | 11 | A | 47.803 | 47.443 | 46.324 | 46.144 | 44.845 |  |  | 44.845 | 45.485 | 46.324 | 46.504 | 47.803 |  | 38.1000 | 95.606 | 10.0000
47.803 |  | G47.803x2.309 | G 1 1/2 | 11 | B | 47.803 | 47.443 | 46.324 | 45.964 | 44.845
53.746 |  | G53.746x2.309 | G 1 3/4 | 11 | A | 53.746 | 53.386 | 52.267 | 52.087 | 50.788 |  |  | 50.788 | 51.428 | 52.267 | 52.447 | 53.746 |  | 44.4500 | 107.492 | 10.0000
53.746 |  | G53.746x2.309 | G 1 3/4 | 11 | B | 53.746 | 53.386 | 52.267 | 51.907 | 50.788
59.614 |  | G59.614x2.309 | G 2 | 11 | A | 59.614 | 59.254 | 58.135 | 57.955 | 56.656 |  |  | 56.656 | 57.296 | 58.135 | 58.315 | 59.614 |  | 50.8000 | 119.228 | 10.0000
59.614 |  | G59.614x2.309 | G 2 | 11 | B | 59.614 | 59.254 | 58.135 | 57.775 | 56.656
65.710 |  | G65.71x2.309 | G 2 1/4 | 11 | A | 65.710 | 65.276 | 64.231 | 64.014 | 62.752 |  |  | 62.752 | 63.392 | 64.231 | 64.448 | 65.710 |  | 57.1500 | 131.420 | 10.0000
65.710 |  | G65.71x2.309 | G 2 1/4 | 11 | B | 65.710 | 65.276 | 64.231 | 63.797 | 62.752
75.184 |  | G75.184x2.309 | G 2 1/2 | 11 | A | 75.184 | 74.750 | 73.705 | 73.488 | 72.226 |  |  | 72.226 | 72.866 | 73.705 | 73.922 | 75.184 |  |  | 150.368 | 10.0000
75.184 |  | G75.184x2.309 | G 2 1/2 | 11 | B | 75.184 | 74.750 | 73.705 | 73.271 | 72.226
81.534 |  | G81.534x2.309 | G 2 3/4 | 11 | A | 81.534 | 81.100 | 80.055 | 79.838 | 78.576 |  |  | 78.576 | 79.216 | 80.055 | 80.272 | 81.534 |  | 69.8500 | 163.068 | 10.0000
81.534 |  | G81.534x2.309 | G 2 3/4 | 11 | B | 81.534 | 81.100 | 80.055 | 79.621 | 78.576
87.884 |  | G87.884x2.309 | G 3 | 11 | A | 87.884 | 87.450 | 86.405 | 86.188 | 84.926 |  |  | 84.926 | 85.566 | 86.405 | 86.622 | 87.884 |  | 76.2000 | 175.768 | 10.0000
87.884 |  | G87.884x2.309 | G 3 | 11 | B | 87.884 | 87.450 | 86.405 | 85.971 | 84.926
100.330 |  | G100.33x2.309 | G 3 1/2 | 11 | A | 100.330 | 99.896 | 98.851 | 98.634 | 97.372 |  |  | 97.372 | 98.012 | 98.851 | 99.068 | 100.330 |  | 88.9000 | 200.660 | 10.0000
100.330 |  | G100.33x2.309 | G 3 1/2 | 11 | B | 100.330 | 99.896 | 98.851 | 98.417 | 97.372
113.030 |  | G113.03x2.309 | G 4 | 11 | A | 113.030 | 112.596 | 111.551 | 111.334 | 110.072 |  |  | 110.072 | 110.712 | 111.551 | 111.768 | 113.030 |  | 101.6000 | 226.060 | 10.0000
113.030 |  | G113.03x2.309 | G 4 | 11 | B | 113.030 | 112.596 | 111.551 | 111.117 | 110.072
125.730 |  | G125.73x2.309 | G 4 1/2 | 11 | A | 125.730 | 125.296 | 124.251 | 124.034 | 122.772 |  |  | 122.772 | 123.412 | 124.251 | 124.468 | 125.730 |  | 114.3000 | 251.460 | 10.0000
125.730 |  | G125.73x2.309 | G 4 1/2 | 11 | B | 125.730 | 125.296 | 124.251 | 123.817 | 122.772
138.430 |  | G138.43x2.309 | G 5 | 11 | A | 138.430 | 137.996 | 136.951 | 136.734 | 135.472 |  |  | 135.472 | 136.112 | 136.951 | 137.168 | 138.430 |  | 127.0000 | 276.860 | 10.0000
138.430 |  | G138.43x2.309 | G 5 | 11 | B | 138.430 | 137.996 | 136.951 | 136.517 | 135.472
151.130 |  | G151.13x2.309 | G 5 1/2 | 11 | A | 151.130 | 150.696 | 149.651 | 149.434 | 148.172 |  |  | 148.172 | 148.812 | 149.651 | 149.868 | 151.130 |  | 139.7000 | 302.260 | 10.0000
151.130 |  | G151.13x2.309 | G 5 1/2 | 11 | B | 151.130 | 150.696 | 149.651 | 149.217 | 148.172
163.830 |  | G163.83x2.309 | G 6 | 11 | A | 163.830 | 163.396 | 162.351 | 162.134 | 160.872 |  |  | 160.872 | 161.512 | 162.351 | 162.568 | 163.830 |  | 152.4000 | 327.660 | 10.0000
163.830 |  | G163.83x2.309 | G 6 | 11 | B | 163.830 | 163.396 | 162.351 | 161.917 | 160.872

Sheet: JIS Pipe Threads
M Q | JIS Pipe Threads |  | Sort Order -12 |  | External |  |  |  |  |  |  | Internal
 |  |  |  |  |  | Major Dia |  | Pitch Dia |  | Minor Dia |  |  | Minor Dia |  | Pitch Dia |  | Major Dia |  | Tap Drill | Thread Depth | Thread Runouts
Size | Size Suffix | Thread Designation | Custom Thread Designation | TPI | Class | Max | Min | Max | Min | Max | Min | Class | Min | Max | Min | Max | Min | Max | Basic |  | Basic
7.723 |  | G7.723x0.907 | G 1/16 | 28 | A | 7.723 | 7.509 | 7.142 | 7.035 | 6.561 |  |  | 6.561 | 6.834 | 7.142 | 7.249 | 7.723 |  | 1.5875 | 15.446 | 4.5000
7.723 |  | G7.723x0.907 | G 1/16 | 28 | B | 7.723 | 7.509 | 7.142 | 6.928 | 6.561
9.728 |  | G9.728x0.907 | G 1/8 | 28 | A | 9.728 | 9.514 | 9.147 | 9.040 | 8.566 |  |  | 8.566 | 8.848 | 9.147 | 9.254 | 9.728 |  | 3.1750 | 19.456 | 4.5000
9.728 |  | G9.728x0.907 | G 1/8 | 28 | B | 9.728 | 9.514 | 9.147 | 8.933 | 8.566
13.157 |  | G13.157x1.337 | G 1/4 | 19 | A | 13.157 | 12.907 | 12.301 | 12.176 | 11.445 |  |  | 11.445 | 11.89 | 12.301 | 12.426 | 13.157 |  | 6.3500 | 26.314 | 6.5000
13.157 |  | G13.157x1.337 | G 1/4 | 19 | B | 13.157 | 12.907 | 12.301 | 12.051 | 11.445
16.662 |  | G16.662x1.337 | G 3/8 | 19 | A | 16.662 | 16.412 | 15.806 | 15.681 | 14.950 |  |  | 14.95 | 15.395 | 15.806 | 15.931 | 16.662 |  | 9.5250 | 33.324 | 6.5000
16.662 |  | G16.662x1.337 | G 3/8 | 19 | B | 16.662 | 16.412 | 15.806 | 15.556 | 14.950
20.955 |  | G20.955x1.814 | G 1/2 | 14 | A | 20.955 | 20.671 | 19.793 | 19.651 | 18.631 |  |  | 18.631 | 19.172 | 19.793 | 19.935 | 20.955 |  | 12.7000 | 41.910 | 8.5000
20.955 |  | G20.955x1.814 | G 1/2 | 14 | B | 20.955 | 20.671 | 19.793 | 19.509 | 18.631
22.911 |  | G22.911x1.814 | G 5/8 | 14 | A | 22.911 | 22.627 | 21.749 | 21.607 | 20.587 |  |  | 20.587 | 21.128 | 21.749 | 21.891 | 22.911 |  |  | 45.822 | 8.5000
22.911 |  | G22.911x1.814 | G 5/8 | 14 | B | 22.911 | 22.627 | 21.749 | 21.465 | 20.587
26.441 |  | G26.441x1.814 | G 3/4 | 14 | A | 26.441 | 26.157 | 25.279 | 25.137 | 24.117 |  |  | 24.117 | 24.658 | 25.279 | 25.421 | 26.441 |  | 15.8750 | 52.882 | 8.5000
26.441 |  | G26.441x1.814 | G 3/4 | 14 | B | 26.441 | 26.157 | 25.279 | 24.995 | 24.117
30.201 |  | G30.201x1.814 | G 7/8 | 14 | A | 30.201 | 29.917 | 29.039 | 28.897 | 27.877 |  |  | 27.877 | 28.418 | 29.039 | 29.181 | 30.201 |  | 22.2250 | 60.402 | 8.8000
30.201 |  | G30.201x1.814 | G 7/8 | 14 | B | 30.201 | 29.917 | 29.039 | 28.755 | 27.877
33.249 |  | G33.249x2.309 | G 1 | 11 | A | 33.249 | 32.889 | 31.770 | 31.590 | 30.291 |  |  | 30.291 | 30.931 | 31.77 | 31.95 | 33.249 |  | 25.4000 | 66.498 | 10.0000
33.249 |  | G33.249x2.309 | G 1 | 11 | B | 33.249 | 32.889 | 31.770 | 31.410 | 30.291
37.897 |  | G37.897x2.309 | G 1 1/8 | 11 | A | 37.897 | 37.537 | 36.418 | 36.238 | 34.939 |  |  | 34.939 | 35.579 | 36.418 | 36.598 | 37.897 |  | 28.5750 | 75.794 | 10.0000
37.897 |  | G37.897x2.309 | G 1 1/8 | 11 | B | 37.897 | 37.537 | 36.418 | 36.058 | 34.939
41.910 |  | G41.91x2.309 | G 1 1/4 | 11 | A | 41.910 | 41.550 | 40.431 | 40.251 | 38.952 |  |  | 38.952 | 39.592 | 40.431 | 40.611 | 41.910 |  | 31.7500 | 83.820 | 10.0000
41.910 |  | G41.91x2.309 | G 1 1/4 | 11 | B | 41.910 | 41.550 | 40.431 | 40.071 | 38.952
47.803 |  | G47.803x2.309 | G 1 1/2 | 11 | A | 47.803 | 47.443 | 46.324 | 46.144 | 44.845 |  |  | 44.845 | 45.485 | 46.324 | 46.504 | 47.803 |  | 38.1000 | 95.606 | 10.0000
47.803 |  | G47.803x2.309 | G 1 1/2 | 11 | B | 47.803 | 47.443 | 46.324 | 45.964 | 44.845
53.746 |  | G53.746x2.309 | G 1 3/4 | 11 | A | 53.746 | 53.386 | 52.267 | 52.087 | 50.788 |  |  | 50.788 | 51.428 | 52.267 | 52.447 | 53.746 |  | 44.4500 | 107.492 | 10.0000
53.746 |  | G53.746x2.309 | G 1 3/4 | 11 | B | 53.746 | 53.386 | 52.267 | 51.907 | 50.788
59.614 |  | G59.614x2.309 | G 2 | 11 | A | 59.614 | 59.254 | 58.135 | 57.955 | 56.656 |  |  | 56.656 | 57.296 | 58.135 | 58.315 | 59.614 |  | 50.8000 | 119.228 | 10.0000
59.614 |  | G59.614x2.309 | G 2 | 11 | B | 59.614 | 59.254 | 58.135 | 57.775 | 56.656
65.710 |  | G65.71x2.309 | G 2 1/4 | 11 | A | 65.710 | 65.276 | 64.231 | 64.014 | 62.752 |  |  | 62.752 | 63.392 | 64.231 | 64.448 | 65.710 |  | 57.1500 | 131.420 | 10.0000
65.710 |  | G65.71x2.309 | G 2 1/4 | 11 | B | 65.710 | 65.276 | 64.231 | 63.797 | 62.752
75.184 |  | G75.184x2.309 | G 2 1/2 | 11 | A | 75.184 | 74.750 | 73.705 | 73.488 | 72.226 |  |  | 72.226 | 72.866 | 73.705 | 73.922 | 75.184 |  |  | 150.368 | 10.0000
75.184 |  | G75.184x2.309 | G 2 1/2 | 11 | B | 75.184 | 74.750 | 73.705 | 73.271 | 72.226
81.534 |  | G81.534x2.309 | G 2 3/4 | 11 | A | 81.534 | 81.100 | 80.055 | 79.838 | 78.576 |  |  | 78.576 | 79.216 | 80.055 | 80.272 | 81.534 |  | 69.8500 | 163.068 | 10.0000
81.534 |  | G81.534x2.309 | G 2 3/4 | 11 | B | 81.534 | 81.100 | 80.055 | 79.621 | 78.576
87.884 |  | G87.884x2.309 | G 3 | 11 | A | 87.884 | 87.450 | 86.405 | 86.188 | 84.926 |  |  | 84.926 | 85.566 | 86.405 | 86.622 | 87.884 |  | 76.2000 | 175.768 | 10.0000
87.884 |  | G87.884x2.309 | G 3 | 11 | B | 87.884 | 87.450 | 86.405 | 85.971 | 84.926
100.330 |  | G100.33x2.309 | G 3 1/2 | 11 | A | 100.330 | 99.896 | 98.851 | 98.634 | 97.372 |  |  | 97.372 | 98.012 | 98.851 | 99.068 | 100.330 |  | 88.9000 | 200.660 | 10.0000
100.330 |  | G100.33x2.309 | G 3 1/2 | 11 | B | 100.330 | 99.896 | 98.851 | 98.417 | 97.372
113.030 |  | G113.03x2.309 | G 4 | 11 | A | 113.030 | 112.596 | 111.551 | 111.334 | 110.072 |  |  | 110.072 | 110.712 | 111.551 | 111.768 | 113.030 |  | 101.6000 | 226.060 | 10.0000
113.030 |  | G113.03x2.309 | G 4 | 11 | B | 113.030 | 112.596 | 111.551 | 111.117 | 110.072
125.730 |  | G125.73x2.309 | G 4 1/2 | 11 | A | 125.730 | 125.296 | 124.251 | 124.034 | 122.772 |  |  | 122.772 | 123.412 | 124.251 | 124.468 | 125.730 |  | 114.3000 | 251.460 | 10.0000
125.730 |  | G125.73x2.309 | G 4 1/2 | 11 | B | 125.730 | 125.296 | 124.251 | 123.817 | 122.772
138.430 |  | G138.43x2.309 | G 5 | 11 | A | 138.430 | 137.996 | 136.951 | 136.734 | 135.472 |  |  | 135.472 | 136.112 | 136.951 | 137.168 | 138.430 |  | 127.0000 | 276.860 | 10.0000
138.430 |  | G138.43x2.309 | G 5 | 11 | B | 138.430 | 137.996 | 136.951 | 136.517 | 135.472
151.130 |  | G151.13x2.309 | G 5 1/2 | 11 | A | 151.130 | 150.696 | 149.651 | 149.434 | 148.172 |  |  | 148.172 | 148.812 | 149.651 | 149.868 | 151.130 |  | 139.7000 | 302.260 | 10.0000
151.130 |  | G151.13x2.309 | G 5 1/2 | 11 | B | 151.130 | 150.696 | 149.651 | 149.217 | 148.172
163.830 |  | G163.83x2.309 | G 6 | 11 | A | 163.830 | 163.396 | 162.351 | 162.134 | 160.872 |  |  | 160.872 | 161.512 | 162.351 | 162.568 | 163.830 |  | 152.4000 | 327.660 | 10.0000
163.830 |  | G163.83x2.309 | G 6 | 11 | B | 163.830 | 163.396 | 162.351 | 161.917 | 160.872

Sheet: DIN Pipe Threads
M Q | DIN Pipe Threads |  | Sort Order - 18 |  | External |  |  |  |  |  |  | Internal
 |  |  |  |  |  | Major Dia |  | Pitch Dia |  | Minor Dia |  |  | Minor Dia |  | Pitch Dia |  | Major Dia |  | Tap Drill | Thread Depth | Thread Runouts
Size | Size Suffix | Thread Designation | Custom Thread Designation | TPI | Class | Max | Min | Max | Min | Max | Min | Class | Min | Max | Min | Max | Min | Max | Basic
7.723 |  | G7.723x0.907 | G 1/16 | 28 | A | 7.723 | 7.509 | 7.142 | 7.035 | 6.561 |  |  | 6.561 | 6.834 | 7.142 | 7.249 | 7.723 |  | 1.5875 | 15.446 | 4.5000
7.723 |  | G7.723x0.907 | G 1/16 | 28 | B | 7.723 | 7.509 | 7.142 | 6.928 | 6.561
9.728 |  | G9.728x0.907 | G 1/8 | 28 | A | 9.728 | 9.514 | 9.147 | 9.040 | 8.566 |  |  | 8.566 | 8.848 | 9.147 | 9.254 | 9.728 |  | 3.1750 | 19.456 | 4.5000
9.728 |  | G9.728x0.907 | G 1/8 | 28 | B | 9.728 | 9.514 | 9.147 | 8.933 | 8.566
13.157 |  | G13.157x1.337 | G 1/4 | 19 | A | 13.157 | 12.907 | 12.301 | 12.176 | 11.445 |  |  | 11.445 | 11.89 | 12.301 | 12.426 | 13.157 |  | 6.3500 | 26.314 | 6.5000
13.157 |  | G13.157x1.337 | G 1/4 | 19 | B | 13.157 | 12.907 | 12.301 | 12.051 | 11.445
16.662 |  | G16.662x1.337 | G 3/8 | 19 | A | 16.662 | 16.412 | 15.806 | 15.681 | 14.950 |  |  | 14.95 | 15.395 | 15.806 | 15.931 | 16.662 |  | 9.5250 | 33.324 | 6.5000
16.662 |  | G16.662x1.337 | G 3/8 | 19 | B | 16.662 | 16.412 | 15.806 | 15.556 | 14.950
20.955 |  | G20.955x1.814 | G 1/2 | 14 | A | 20.955 | 20.671 | 19.793 | 19.651 | 18.631 |  |  | 18.631 | 19.172 | 19.793 | 19.935 | 20.955 |  | 12.7000 | 41.910 | 8.5000
20.955 |  | G20.955x1.814 | G 1/2 | 14 | B | 20.955 | 20.671 | 19.793 | 19.509 | 18.631
22.911 |  | G22.911x1.814 | G 5/8 | 14 | A | 22.911 | 22.627 | 21.749 | 21.607 | 20.587 |  |  | 20.587 | 21.128 | 21.749 | 21.891 | 22.911 |  |  | 45.822 | 8.5000
22.911 |  | G22.911x1.814 | G 5/8 | 14 | B | 22.911 | 22.627 | 21.749 | 21.465 | 20.587
26.441 |  | G26.441x1.814 | G 3/4 | 14 | A | 26.441 | 26.157 | 25.279 | 25.137 | 24.117 |  |  | 24.117 | 24.658 | 25.279 | 25.421 | 26.441 |  | 15.8750 | 52.882 | 8.5000
26.441 |  | G26.441x1.814 | G 3/4 | 14 | B | 26.441 | 26.157 | 25.279 | 24.995 | 24.117
30.201 |  | G30.201x1.814 | G 7/8 | 14 | A | 30.201 | 29.917 | 29.039 | 28.897 | 27.877 |  |  | 27.877 | 28.418 | 29.039 | 29.181 | 30.201 |  | 22.2250 | 60.402 | 8.5000
30.201 |  | G30.201x1.814 | G 7/8 | 14 | B | 30.201 | 29.917 | 29.039 | 28.755 | 27.877
33.249 |  | G33.249x2.309 | G 1 | 11 | A | 33.249 | 32.889 | 31.770 | 31.590 | 30.291 |  |  | 30.291 | 30.931 | 31.77 | 31.95 | 33.249 |  | 25.4000 | 66.498 | 10.5000
33.249 |  | G33.249x2.309 | G 1 | 11 | B | 33.249 | 32.889 | 31.770 | 31.410 | 30.291
37.897 |  | G37.897x2.309 | G 1 1/8 | 11 | A | 37.897 | 37.537 | 36.418 | 36.238 | 34.939 |  |  | 34.939 | 35.579 | 36.418 | 36.598 | 37.897 |  | 28.5750 | 75.794 | 10.5000
37.897 |  | G37.897x2.309 | G 1 1/8 | 11 | B | 37.897 | 37.537 | 36.418 | 36.058 | 34.939
41.910 |  | G41.91x2.309 | G 1 1/4 | 11 | A | 41.910 | 41.550 | 40.431 | 40.251 | 38.952 |  |  | 38.952 | 39.592 | 40.431 | 40.611 | 41.910 |  | 31.7500 | 83.820 | 10.5000
41.910 |  | G41.91x2.309 | G 1 1/4 | 11 | B | 41.910 | 41.550 | 40.431 | 40.071 | 38.952
47.803 |  | G47.803x2.309 | G 1 1/2 | 11 | A | 47.803 | 47.443 | 46.324 | 46.144 | 44.845 |  |  | 44.845 | 45.485 | 46.324 | 46.504 | 47.803 |  | 38.1000 | 95.606 | 10.5000
47.803 |  | G47.803x2.309 | G 1 1/2 | 11 | B | 47.803 | 47.443 | 46.324 | 45.964 | 44.845
53.746 |  | G53.746x2.309 | G 1 3/4 | 11 | A | 53.746 | 53.386 | 52.267 | 52.087 | 50.788 |  |  | 50.788 | 51.428 | 52.267 | 52.447 | 53.746 |  | 44.4500 | 107.492 | 10.5000
53.746 |  | G53.746x2.309 | G 1 3/4 | 11 | B | 53.746 | 53.386 | 52.267 | 51.907 | 50.788
59.614 |  | G59.614x2.309 | G 2 | 11 | A | 59.614 | 59.254 | 58.135 | 57.955 | 56.656 |  |  | 56.656 | 57.296 | 58.135 | 58.315 | 59.614 |  | 50.8000 | 119.228 | 10.5000
59.614 |  | G59.614x2.309 | G 2 | 11 | B | 59.614 | 59.254 | 58.135 | 57.775 | 56.656
65.710 |  | G65.71x2.309 | G 2 1/4 | 11 | A | 65.710 | 65.276 | 64.231 | 64.014 | 62.752 |  |  | 62.752 | 63.392 | 64.231 | 64.448 | 65.710 |  | 57.1500 | 131.420 | 10.5000
65.710 |  | G65.71x2.309 | G 2 1/4 | 11 | B | 65.710 | 65.276 | 64.231 | 63.797 | 62.752
75.184 |  | G75.184x2.309 | G 2 1/2 | 11 | A | 75.184 | 74.750 | 73.705 | 73.488 | 72.226 |  |  | 72.226 | 72.866 | 73.705 | 73.922 | 75.184 |  |  | 150.368 | 10.5000
75.184 |  | G75.184x2.309 | G 2 1/2 | 11 | B | 75.184 | 74.750 | 73.705 | 73.271 | 72.226
81.534 |  | G81.534x2.309 | G 2 3/4 | 11 | A | 81.534 | 81.100 | 80.055 | 79.838 | 78.576 |  |  | 78.576 | 79.216 | 80.055 | 80.272 | 81.534 |  | 69.8500 | 163.068 | 10.5000
81.534 |  | G81.534x2.309 | G 2 3/4 | 11 | B | 81.534 | 81.100 | 80.055 | 79.621 | 78.576
87.884 |  | G87.884x2.309 | G 3 | 11 | A | 87.884 | 87.450 | 86.405 | 86.188 | 84.926 |  |  | 84.926 | 85.566 | 86.405 | 86.622 | 87.884 |  | 76.2000 | 175.768 | 10.5000
87.884 |  | G87.884x2.309 | G 3 | 11 | B | 87.884 | 87.450 | 86.405 | 85.971 | 84.926
100.330 |  | G100.33x2.309 | G 3 1/2 | 11 | A | 100.330 | 99.896 | 98.851 | 98.634 | 97.372 |  |  | 97.372 | 98.012 | 98.851 | 99.068 | 100.330 |  | 88.9000 | 200.660 | 10.5000
100.330 |  | G100.33x2.309 | G 3 1/2 | 11 | B | 100.330 | 99.896 | 98.851 | 98.417 | 97.372
113.030 |  | G113.03x2.309 | G 4 | 11 | A | 113.030 | 112.596 | 111.551 | 111.334 | 110.072 |  |  | 110.072 | 110.712 | 111.551 | 111.768 | 113.030 |  | 101.6000 | 226.060 | 10.5000
113.030 |  | G113.03x2.309 | G 4 | 11 | B | 113.030 | 112.596 | 111.551 | 111.117 | 110.072
125.730 |  | G125.73x2.309 | G 4 1/2 | 11 | A | 125.730 | 125.296 | 124.251 | 124.034 | 122.772 |  |  | 122.772 | 123.412 | 124.251 | 124.468 | 125.730 |  | 114.3000 | 251.460 | 10.5000
125.730 |  | G125.73x2.309 | G 4 1/2 | 11 | B | 125.730 | 125.296 | 124.251 | 123.817 | 122.772
138.430 |  | G138.43x2.309 | G 5 | 11 | A | 138.430 | 137.996 | 136.951 | 136.734 | 135.472 |  |  | 135.472 | 136.112 | 136.951 | 137.168 | 138.430 |  | 127.0000 | 276.860 | 10.5000
138.430 |  | G138.43x2.309 | G 5 | 11 | B | 138.430 | 137.996 | 136.951 | 136.517 | 135.472
151.130 |  | G151.13x2.309 | G 5 1/2 | 11 | A | 151.130 | 150.696 | 149.651 | 149.434 | 148.172 |  |  | 148.172 | 148.812 | 149.651 | 149.868 | 151.130 |  | 139.7000 | 302.260 | 10.5000
151.130 |  | G151.13x2.309 | G 5 1/2 | 11 | B | 151.130 | 150.696 | 149.651 | 149.217 | 148.172
163.830 |  | G163.83x2.309 | G 6 | 11 | A | 163.830 | 163.396 | 162.351 | 162.134 | 160.872 |  |  | 160.872 | 161.512 | 162.351 | 162.568 | 163.830 |  | 152.4000 | 327.660 | 10.5000
163.830 |  | G163.83x2.309 | G 6 | 11 | B | 163.830 | 163.396 | 162.351 | 161.917 | 160.872

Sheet: BSP Pipe Threads
M Q | BSP Pipe Threads |  | Sort Order - 19 |  | External |  |  |  |  |  |  | Internal
 |  |  |  |  |  | Major Dia |  | Pitch Dia |  | Minor Dia |  |  | Minor Dia |  | Pitch Dia |  | Major Dia |  | Tap Drill | Thread Depth | Thread Runouts
Size | Size Suffix | Thread Designation | Custom Thread Designation | TPI | Class | Max | Min | Max | Min | Max | Min | Class | Min | Max | Min | Max | Min | Max | Basic |  | Basic
1/16 |  | G 1/16-28 | G 1/16-28 | 28 | A | 7.723 | 7.509 | 7.142 | 7.035 | 6.561 |  |  | 6.561 | 6.834 | 7.142 | 7.249 | 7.723 |  | 6.6000 | 15.4460 | 4.5000
1/16 |  | G 1/16-28 | G 1/16-28 | 28 | B | 7.723 | 7.509 | 7.142 | 7.035 | 6.561
1/8 |  | G 1/8-28 | G 1/8-28 | 28 | A | 9.728 | 9.514 | 9.147 | 9.040 | 8.566 |  |  | 8.566 | 8.848 | 9.147 | 9.254 | 9.728 |  | 8.7300 | 19.4560 | 4.5000
1/8 |  | G 1/8-28 | G 1/8-28 | 28 | B | 9.728 | 9.514 | 9.147 | 9.040 | 8.566
1/4 |  | G 1/4-19 | G 1/4-19 | 19 | A | 13.157 | 12.907 | 12.301 | 12.176 | 11.445 |  |  | 11.445 | 11.89 | 12.301 | 12.426 | 13.157 |  | 11.8000 | 26.3140 | 6.5000
1/4 |  | G 1/4-19 | G 1/4-19 | 19 | B | 13.157 | 12.907 | 12.301 | 12.176 | 11.445
3/8 |  | G 3/8-19 | G 3/8-19 | 19 | A | 16.662 | 16.412 | 15.806 | 15.681 | 14.950 |  |  | 14.95 | 15.395 | 15.806 | 15.931 | 16.662 |  | 15.2500 | 33.3240 | 6.5000
3/8 |  | G 3/8-19 | G 3/8-19 | 19 | B | 16.662 | 16.412 | 15.806 | 15.681 | 14.950
1/2 |  | G 1/2-14 | G 1/2-14 | 14 | A | 20.955 | 20.671 | 19.793 | 19.651 | 18.631 |  |  | 18.631 | 19.172 | 19.793 | 19.935 | 20.955 |  | 19.0500 | 41.9100 | 8.5000
1/2 |  | G 1/2-14 | G 1/2-14 | 14 | B | 20.955 | 20.671 | 19.793 | 19.651 | 18.631
5/8 |  | G 5/8-14 | G 5/8-14 | 14 | A | 22.911 | 22.627 | 21.749 | 21.607 | 20.587 |  |  | 20.587 | 21.128 | 21.749 | 21.891 | 22.911 |  | 21.0000 | 45.8220 | 8.5000
5/8 |  | G 5/8-14 | G 5/8-14 | 14 | B | 22.911 | 22.627 | 21.749 | 21.607 | 20.587
3/4 |  | G 3/4-14 | G 3/4-14 | 14 | A | 26.441 | 26.157 | 25.279 | 25.137 | 24.117 |  |  | 24.117 | 24.658 | 25.279 | 25.421 | 26.441 |  | 24.5000 | 52.8820 | 8.5000
3/4 |  | G 3/4-14 | G 3/4-14 | 14 | B | 26.441 | 26.157 | 25.279 | 25.137 | 24.117
7/8 |  | G 7/8-14 | G 7/8-14 | 14 | A | 30.201 | 29.917 | 29.039 | 28.897 | 27.877 |  |  | 27.877 | 28.418 | 29.039 | 29.181 | 30.201 |  | 28.2500 | 60.4020 | 8.5000
7/8 |  | G 7/8-14 | G 7/8-14 | 14 | B | 30.201 | 29.917 | 29.039 | 28.897 | 27.877
1 |  | G 1-11 | G 1-11 | 11 | A | 33.249 | 32.889 | 31.770 | 31.590 | 30.291 |  |  | 30.291 | 30.931 | 31.77 | 31.95 | 33.249 |  | 30.7500 | 66.4980 | 10.0000
1 |  | G 1-11 | G 1-11 | 11 | B | 33.249 | 32.889 | 31.770 | 31.590 | 30.291
1 1/4 |  | G 1 1/4-11 | G 1 1/4-11 | 11 | A | 41.910 | 41.550 | 40.431 | 40.251 | 38.952 |  |  | 38.952 | 39.592 | 40.431 | 40.611 | 41.910 |  | 39.5000 | 83.8200 | 10.0000
1 1/4 |  | G 1 1/4-11 | G 1 1/4-11 | 11 | B | 41.910 | 41.550 | 40.431 | 40.251 | 38.952
1 1/2 |  | G 1 1/2-11 | G 1 1/2-11 | 11 | A | 47.803 | 47.443 | 46.324 | 46.144 | 44.845 |  |  | 44.845 | 45.485 | 46.324 | 46.504 | 47.803 |  | 45.5000 | 95.6060 | 10.0000
1 1/2 |  | G 1 1/2-11 | G 1 1/2-11 | 11 | B | 47.803 | 47.443 | 46.324 | 46.144 | 44.845
1 3/4 |  | G 1 3/4-11 | G 1 3/4-11 | 11 | A | 53.746 | 53.386 | 52.267 | 52.087 | 50.788 |  |  | 50.788 | 51.428 | 52.267 | 52.447 | 53.746 |  | 51.0000 | 107.4920 | 10.0000
1 3/4 |  | G 1 3/4-11 | G 1 3/4-11 | 11 | B | 53.746 | 53.386 | 52.267 | 52.087 | 50.788
2 |  | G 2-11 | G 2-11 | 11 | A | 59.614 | 59.254 | 58.135 | 57.955 | 56.656 |  |  | 56.656 | 57.296 | 58.135 | 58.315 | 59.614 |  | 57.0000 | 119.2280 | 10.0000
2 |  | G 2-11 | G 2-11 | 11 | B | 59.614 | 59.254 | 58.135 | 57.955 | 56.656
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

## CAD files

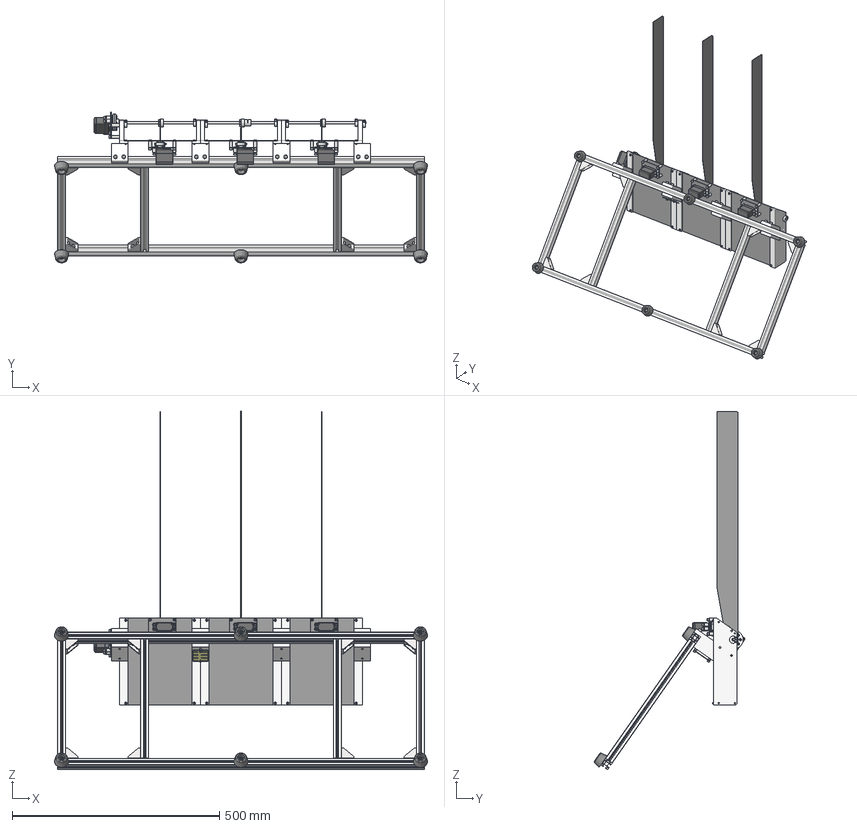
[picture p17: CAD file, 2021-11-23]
assy-shooter/assy-shooter.stp
899.0 x 363.2 x 863.0 mm
s_carbon_plate4
Top x 4
Medio x 4
Base x 4
Eje x 4
horn x 4
ARF-410E x 16
CB4-6 x 31
CBSTSR4-6 x 28
CB3-5 x 6
unir-spacer4 x 3
CB4-10 x 3
s_carbon_plate5 x 3
SCSTR6-8b x 4
BOLT3-12 x 4
CB3-8 x 17
D_CPRC16-6-6
M2.5 x 2
s_base6
s_base5
CB3-6 x 4
CB3-10 x 10
LBNR3 x 41
CC-0612-05
SFR6-285_s
SFR6-321
NFS5-2020-885 x 2
NFS5-2020-351 x 4
HBLFSN5h5 x 8
HNTT5-5 x 38
CB5-10 x 16
K-34 x 6
CB5-12 x 6
HNTC5_n x 8
Hexagon socket set screw with flat point DIN 913 - M4x4 x 8
shooter_base7 x 7
MF126ZZ x 8
d_type_board
s_base1 x 4
SB-305060 x 24
CB5-15 x 8
CB5-40 x 8
s_carbon_plate1 x 3
s_base4 x 3
s_base1_1 x 3
s_base3 x 3
s_carbon_plate2 x 3
CB3-25 x 6
CBSTSR3-10 x 36
s_carbon_plate8 x 3
ARF-415 x 12
CB3-15 x 8
hexagonal_spacer_M3_5mm x 2

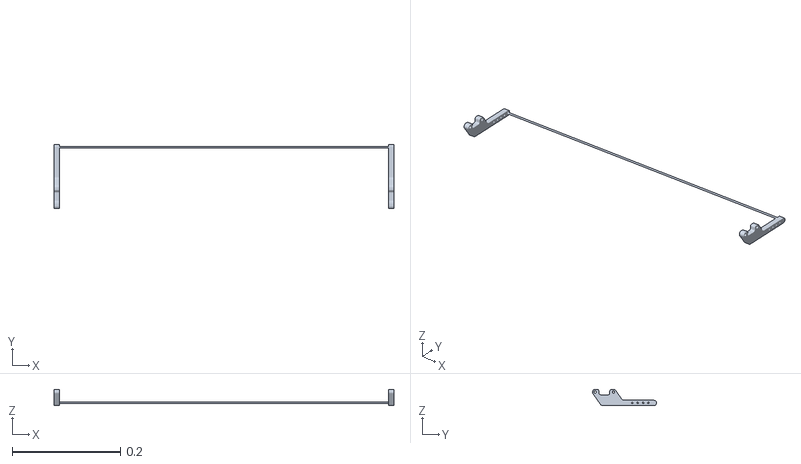
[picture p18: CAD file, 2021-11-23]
assy-scara/s-assy-guide.stl
0.627 x 0.118 x 0.03

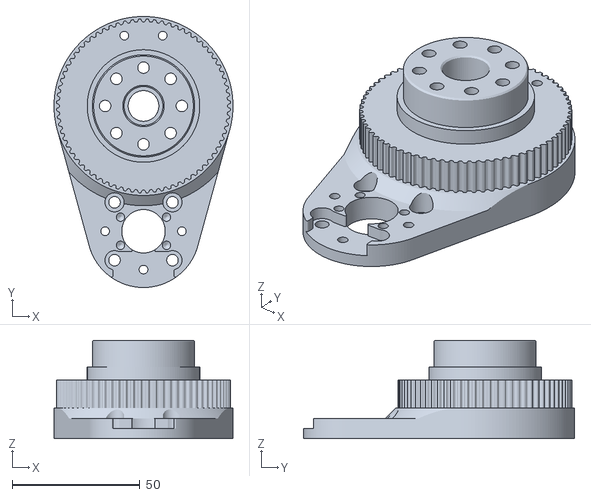
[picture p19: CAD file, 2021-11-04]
3d_print/scara-base20.stl
70.0 x 106.0 x 38.5

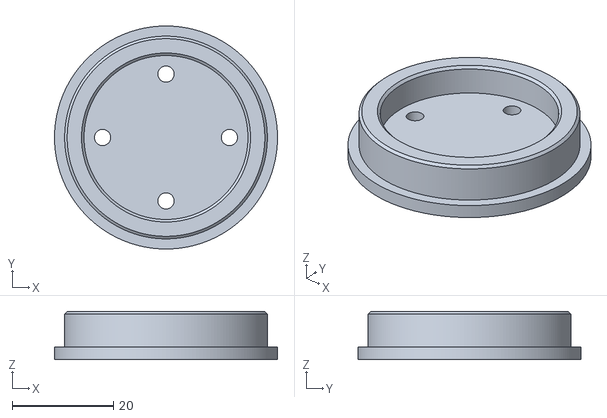
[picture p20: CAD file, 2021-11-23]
assy-scara/3d print/base13.stl
44.0 x 44.0 x 9.50

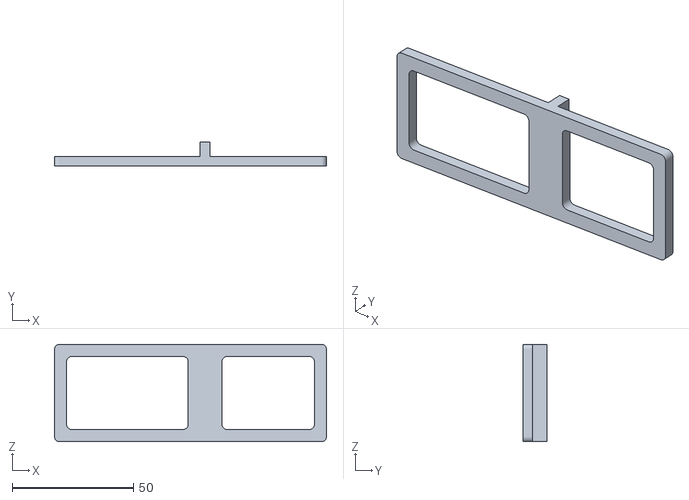
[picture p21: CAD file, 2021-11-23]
assy-scara/Part2.stl
112.0 x 10.0 x 40.0

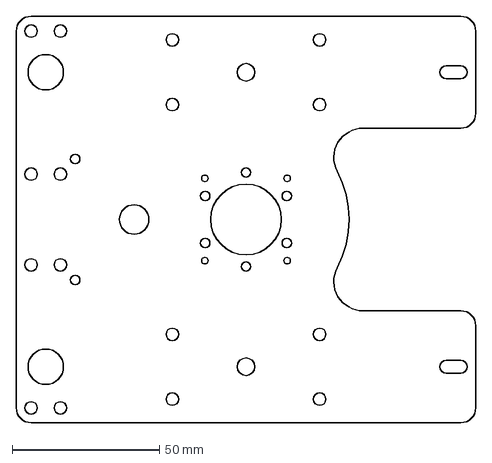
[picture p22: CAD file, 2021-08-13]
carbon_plate_dxf/carbon_plate14.dxf
156.0 x 138.0 mm

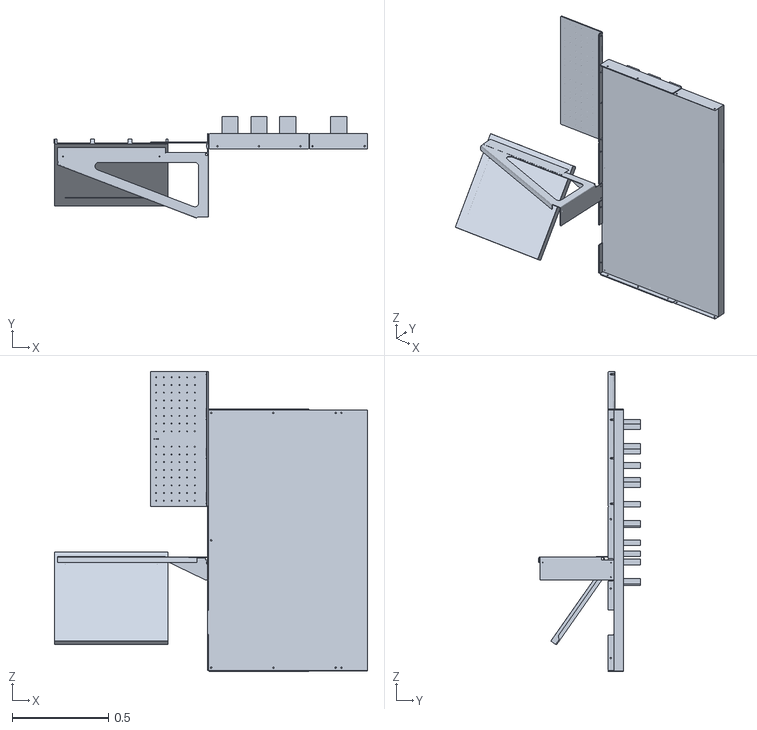
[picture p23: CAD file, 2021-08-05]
field/blue_side.stl
1.62 x 0.527 x 1.56

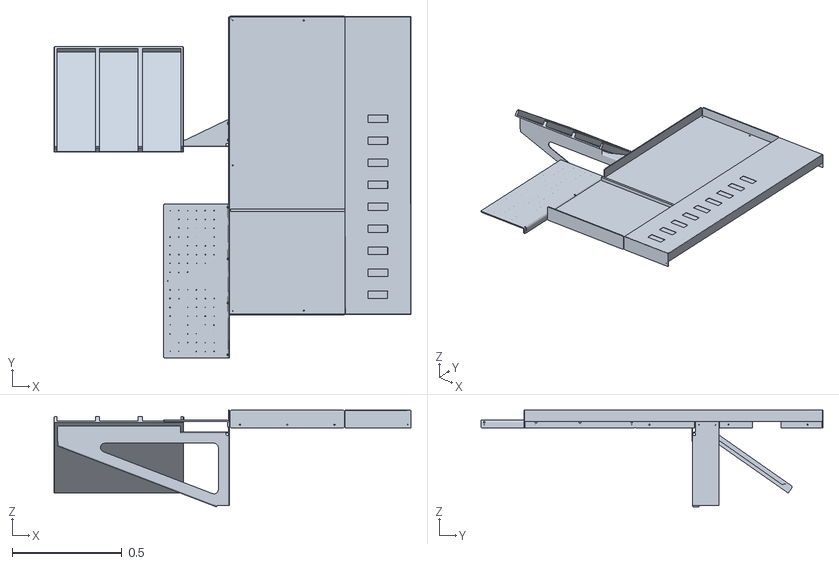
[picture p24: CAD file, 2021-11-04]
mesh/base/collision/base_blue_plane.stl
1.62 x 1.56 x 0.441

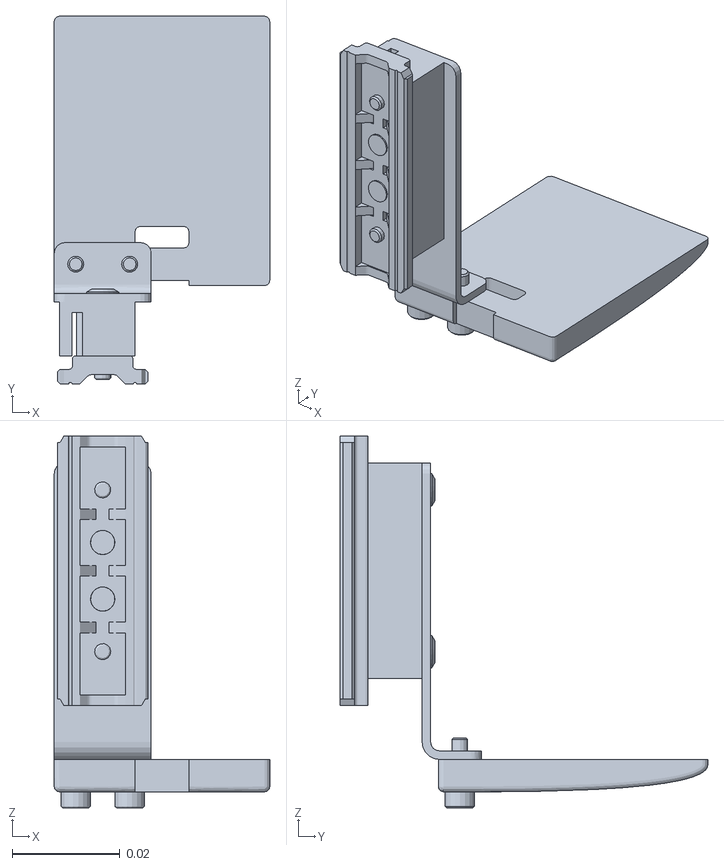
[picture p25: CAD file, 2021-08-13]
mesh/detailed/finger.stl
0.04 x 0.0682 x 0.069

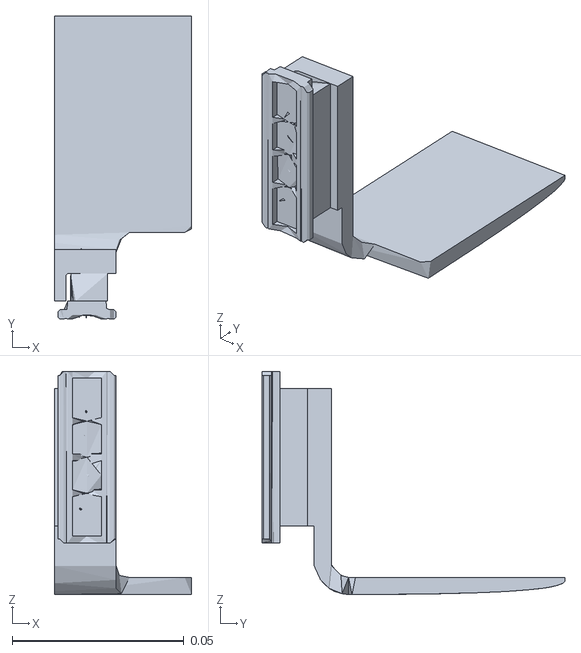
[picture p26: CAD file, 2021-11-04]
mesh/scara/collision/gripper_finger.stl
0.04 x 0.0882 x 0.065

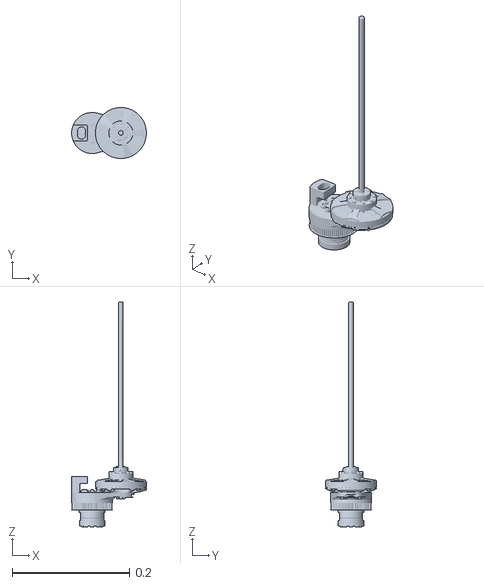
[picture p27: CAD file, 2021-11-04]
mesh/scara/visual/link3.stl
0.127 x 0.087 x 0.384

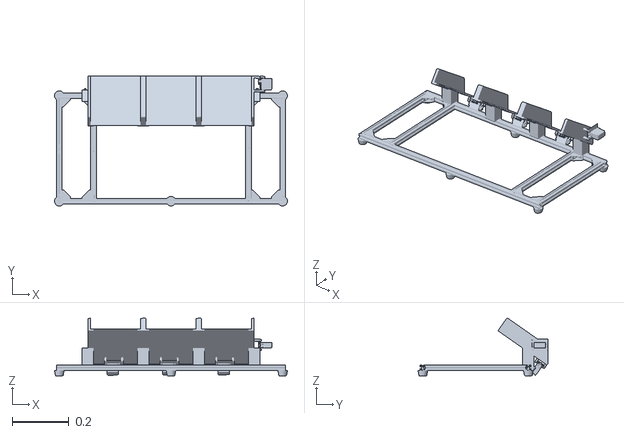
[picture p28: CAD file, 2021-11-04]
mesh/shooter/collision/base.stl
0.819 x 0.457 x 0.203

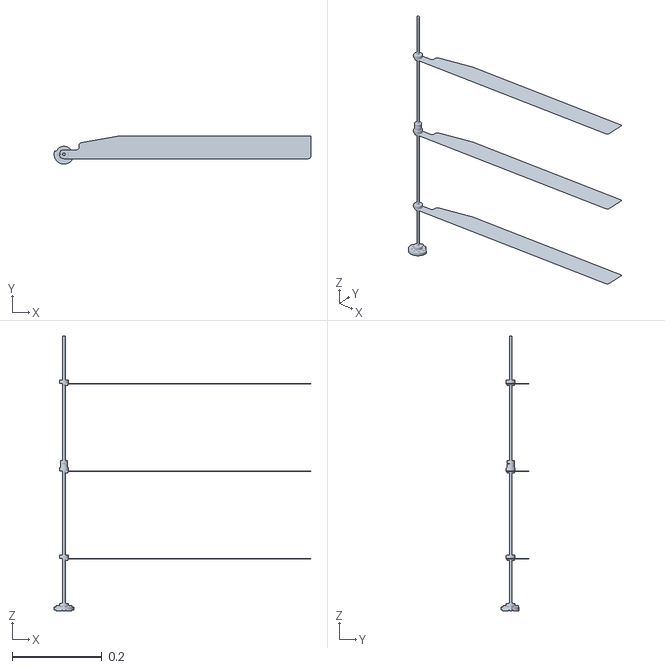
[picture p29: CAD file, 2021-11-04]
mesh/shooter/visual/guide.stl
0.572 x 0.063 x 0.613

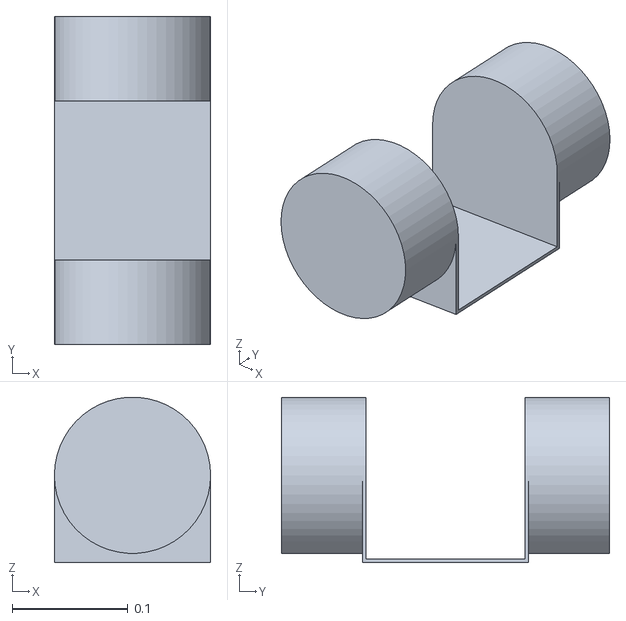
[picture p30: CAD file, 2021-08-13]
mesh/simple/link1.stl
0.135 x 0.283 x 0.143

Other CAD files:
assy-scara/Templates/English/ANSI (in).dwg
assy-scara/Templates/Metric/ISO.dwg
assy-scara/Templates/Standard.dwg
mesh/base/visual/base_red_plane.stl
3d_print/Assembly1.iam
3d_print/OldVersions/Assembly1.0001.iam
3d_print/Part1.ipt
3d_print/assy-robot.idw
3d_print/base1.stl
3d_print/base10.stl
3d_print/base11.stl
3d_print/base12.stl
3d_print/base13-1.stl
3d_print/base13-2.stl
3d_print/base14-1.stl
3d_print/base14-2.stl
3d_print/base15_2.stl
3d_print/base15_3.stl
3d_print/base16.stl
3d_print/base17.stl
3d_print/base18.stl
3d_print/base19.stl
3d_print/base2.stl
3d_print/base20-1.stl
3d_print/base20-2.stl
3d_print/base20.stl
3d_print/base21.stl
3d_print/base23.stl
3d_print/base24.stl
3d_print/base25.stl
3d_print/base26.stl
3d_print/base27.stl
3d_print/base28.stl
3d_print/base29.stl
3d_print/base3.stl
3d_print/base30.stl
3d_print/base31.stl
3d_print/base32.stl
3d_print/base33.stl
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

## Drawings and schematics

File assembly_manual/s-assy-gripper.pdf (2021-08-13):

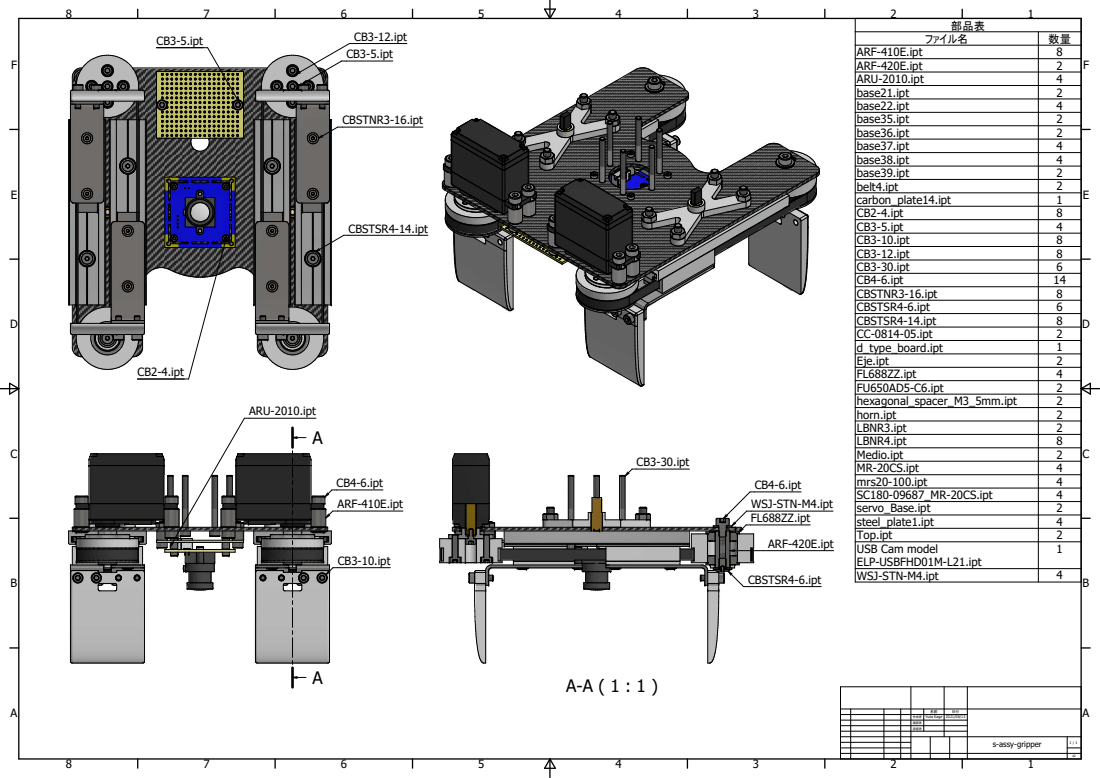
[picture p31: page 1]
s-assy-gripper; Yuta Kage 2021/08/13; 作成者; 確認者; 承認者; 部品表; ファイル名; ARF-410E.ipt; ARF-420E.ipt; ARU-2010.ipt; base21.ipt; base22.ipt; base35.ipt; base36.ipt; base37.ipt; base38.ipt; base39.ipt; belt4.ipt; carbon_plate14.ipt; CB2-4.ipt; CB3-5.ipt; CB3-10.ipt; CB3-12.ipt; CB3-30.ipt; CB4-6.ipt; CBSTNR3-16.ipt; CBSTSR4-6.ipt; CBSTSR4-14.ipt; CC-0814-05.ipt; d_type_board.ipt; Eje.ipt; FL688ZZ.ipt; FU650AD5-C6.ipt; hexagonal_spacer_M3_5mm.ipt; horn.ipt; LBNR3.ipt; LBNR4.ipt; Medio.ipt; MR-20CS.ipt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

CB4-6.ipt
WSJ-STN-M4.ipt
FL688ZZ.ipt

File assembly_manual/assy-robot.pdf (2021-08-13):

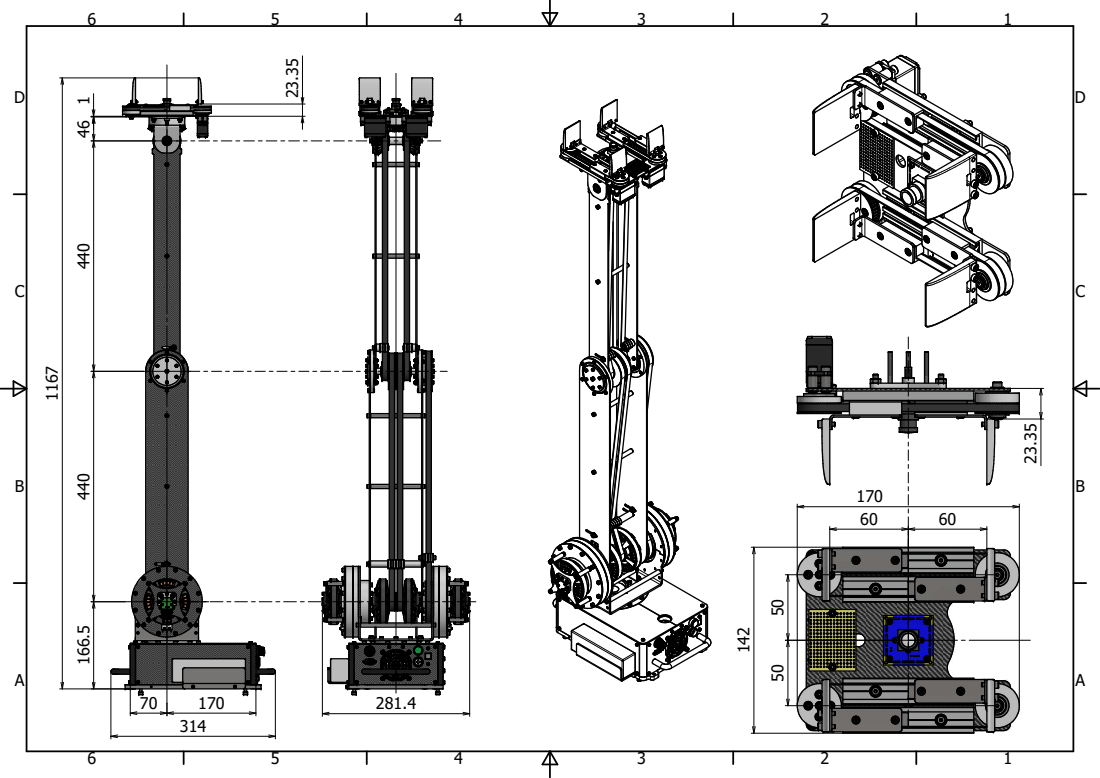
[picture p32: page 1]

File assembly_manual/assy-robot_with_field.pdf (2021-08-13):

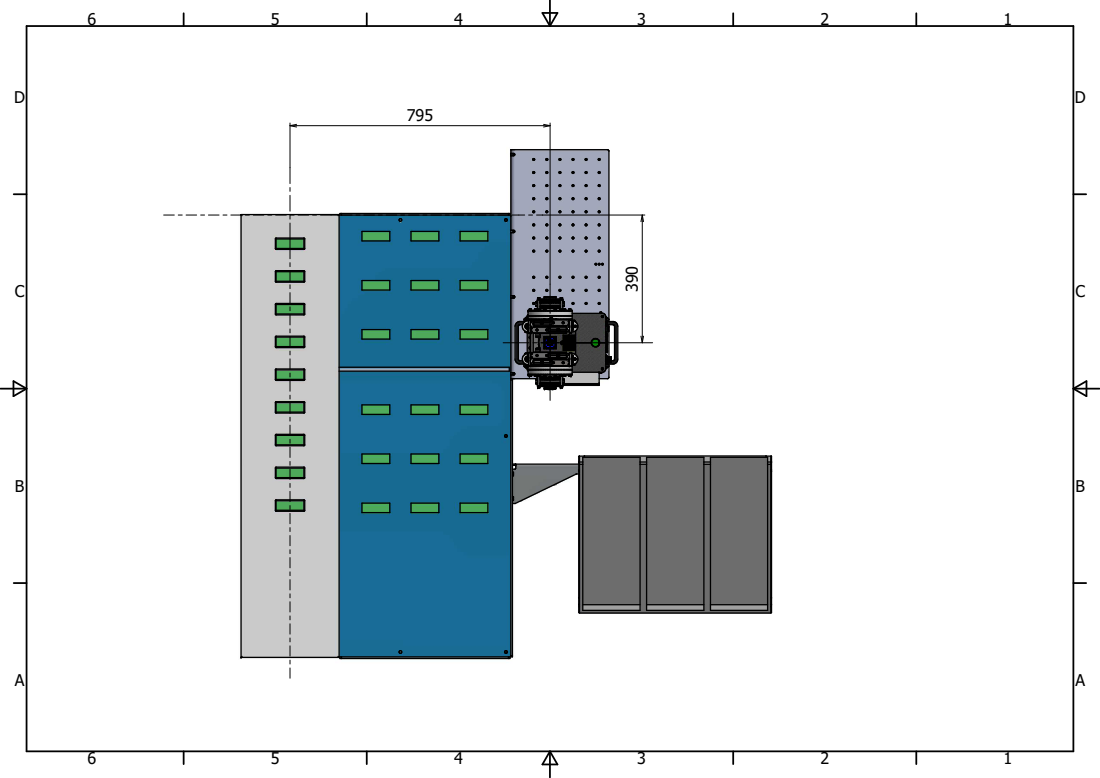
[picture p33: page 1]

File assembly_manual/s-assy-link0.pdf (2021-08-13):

A

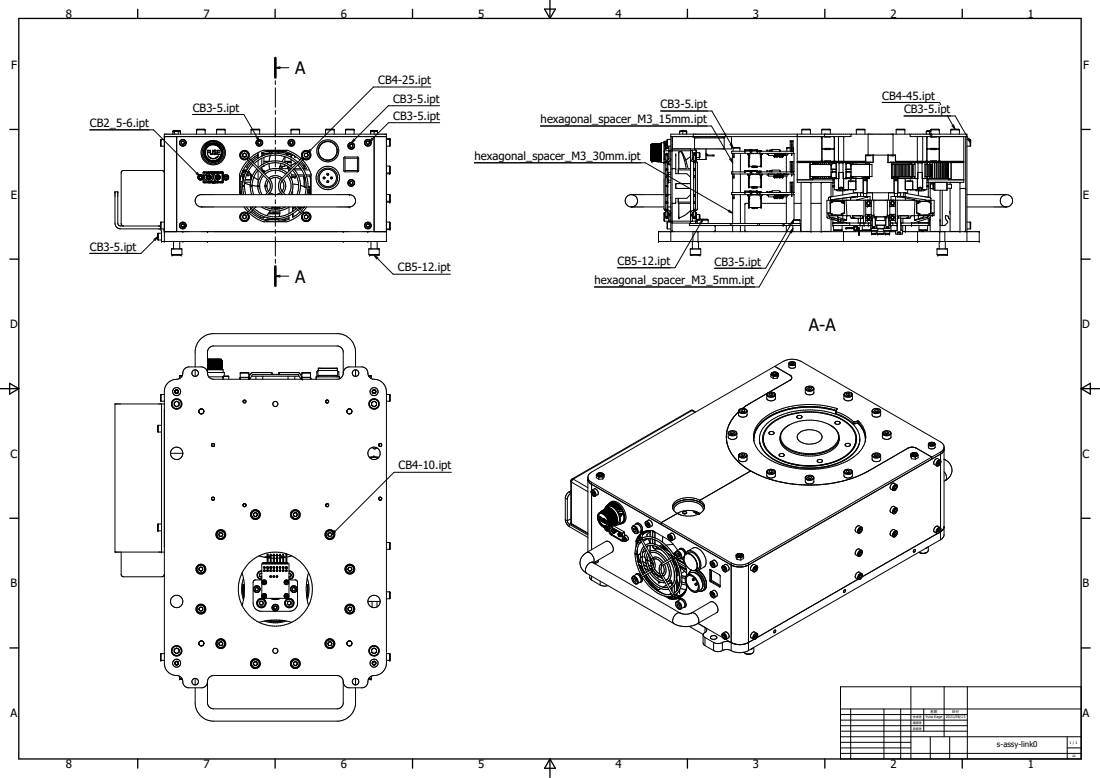
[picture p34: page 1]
s-assy-link0; Yuta Kage 2021/08/13; 作成者; 確認者; 承認者; CB3-5.ipt; CB4-25.ipt; CB2_5-6.ipt; CB5-12.ipt; CB3-5.ipt hexagonal_spacer_M3_15mm.ipt; hexagonal_spacer_M3_30mm.ipt; hexagonal_spacer_M3_5mm.ipt; CB4-45.ipt CB3-5.ipt; CB4-10.ipt

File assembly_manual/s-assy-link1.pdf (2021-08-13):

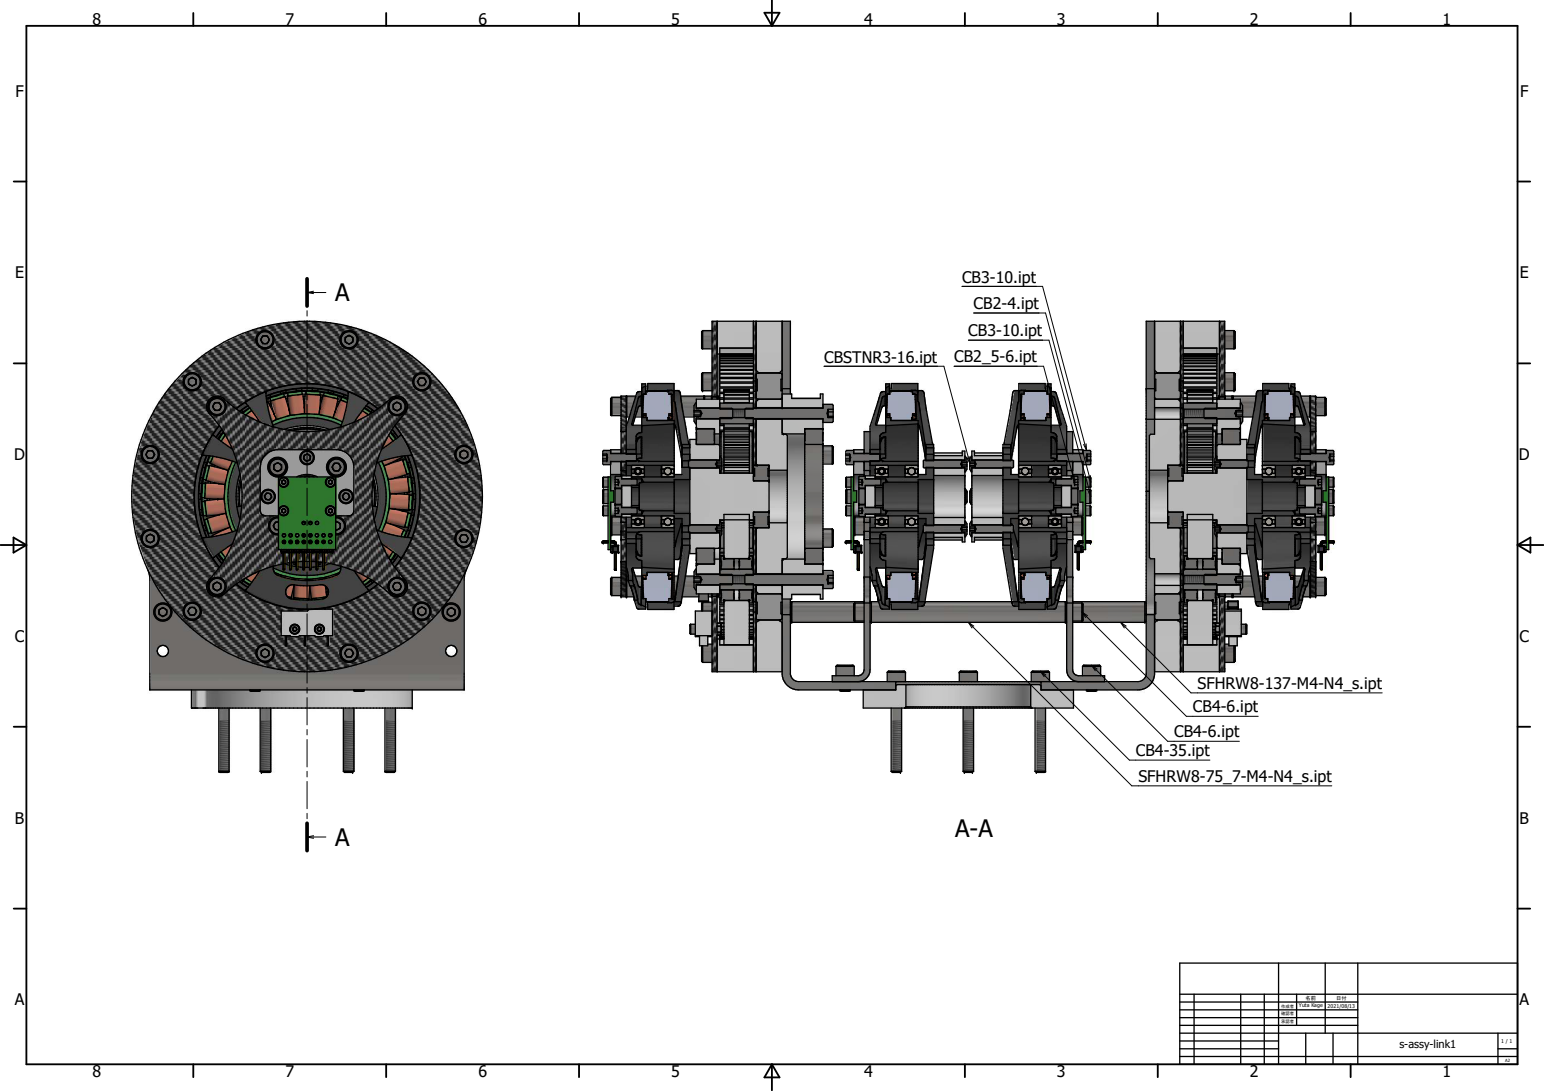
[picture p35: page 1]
s-assy-link1; Yuta Kage 2021/08/13; 作成者; 確認者; 承認者; CB3-10.ipt; CB2-4.ipt; CBSTNR3-16.ipt CB2_5-6.ipt; SFHRW8-75_7-M4-N4_s.ipt; CB4-6.ipt; SFHRW8-137-M4-N4_s.ipt; CB4-6.ipt CB4-35.ipt

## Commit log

2021-08-05 cad update
    [010_U8_ROTOR.ipt, 020_U8_STATOR_HOUSING.ipt, 021_U8_STATOR_COILS.ipt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]
2021-08-28 update shooting box
    [ARF-415.0001.ipt, ARF-415.ipt, Assembly1.0003.iam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]
2021-09-06 1st version
    [Assembly1.0001.iam, Assembly1.iam, assy-robot.idw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]
2021-10-06 shooter ready
    [234_C4_2020.0001.iam, 234_C4_2020.iam, ANSI (in).dwg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]
2021-10-06 shooter with controller ready
    [K-34.step, assy-shooter.0437.iam, assy-shooter.0447.iam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]
2021-11-04 scara update
    [010_U8_ROTOR.0014.ipt, 010_U8_ROTOR.ipt, 020_U8_STATOR_HOUSING.0004.ipt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]
2021-11-23 final update
    [234_C4_2020.0005.iam, 234_C4_2020.0006.iam, 234_C4_2020.iam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]
